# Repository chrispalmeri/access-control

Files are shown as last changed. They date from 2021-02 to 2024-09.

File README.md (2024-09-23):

# doorctl

DIY door access control system with NanoPi

Software part is very much unfinished

<!--

order spare inventory parts

board changes:
  put 12V at the top, move lock?
  you meant to widen lock trace
  you could make the JLCJLC text bigger
  and the github text
  any way to get the resistor designators readable? smaller?
  upsidedown ethernet kinda bugs me

python
  update docs
  totp

-->

# Hardware

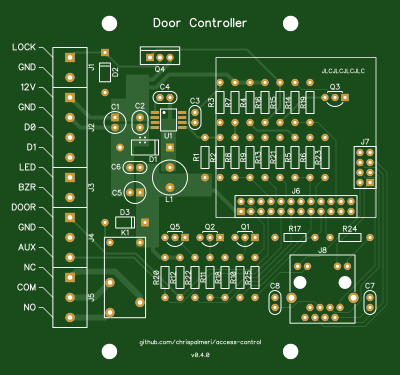
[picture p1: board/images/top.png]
Board picture


[DipTrace][1] files, `gerber.zip` works with [JLCPCB][2]

Removed SVG's from repo but you can drop `gerber.zip` into [tracespace][3] to generate.

You need to plug a [NanoPi Neo Core][4] on to it

  [1]: https://diptrace.com/
  [2]: https://jlcpcb.com/
  [3]: https://tracespace.io/view/
  [4]: https://www.friendlyelec.com/index.php?route=product/product&path=69&product_id=212

These are the gpio pins that are used:

Name | Physical | libgpiod | Type | Description
---  | ---      | ---      | ---  | ---
PA1  | 22       | 1        | OUT  | lock
PG8  | 16       | 200      | OUT  | relay out
PG9  | 18       | 201      | OUT  | reader led
PA6  | 12       | 6        | OUT  | reader buzzer
PA3  | 15       | 3        | IN   | reader d0
PG11 | 7        | 203      | IN   | reader d1
PG6  | 8        | 198      | IN   | door contact
PG7  | 10       | 199      | IN   | doorbell

# Software

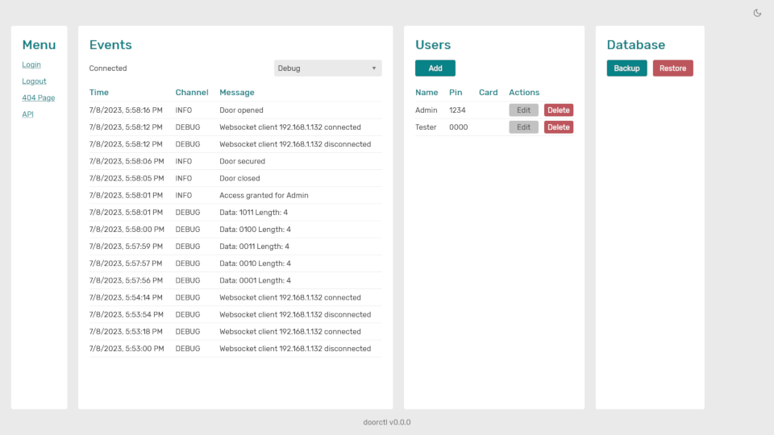
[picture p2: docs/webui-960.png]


## Preparation

Download [Armbian][5] Bullseye CLI image (get the latest archive version),
use [Etcher][6] to flash the image onto your [SD card][7].

Install the SD card and power up the board.

  [5]: https://www.armbian.com/nanopi-neo/
  [6]: https://etcher.balena.io/
  [7]: https://www.westerndigital.com/products/memory-cards/sandisk-ultra-uhs-i-microsd#SDSQUA4-032G-GN6MA

## First boot

Use [Windows Terminal][8] to `ssh root@nanopineo` and login with password `1234`.

* enter new root password twice
* pick `1` for "bash" terminal
* enter new username (e.g. `doorctl`)
* password twice
* display name
* `Enter` to accept language based on detected timezone
* pick `1` for "en_US.UTF-8"
* Run `armbian-config`
    * Personal > Hostname > type a new hostname (e.g. `doorctl-dev`) > Ok > Back
    * System > Install > Install/Update the bootloader on SD/eMMC > Yes
    * System > Install > Boot from eMMC - system on eMMC > Yes > ext4 > Power Off

Unplug power, Remove SD card.

  [8]: https://apps.microsoft.com/store/detail/windows-terminal/9N0DX20HK701

<!--
I think you could then reuse the SD card on additional boards
and only need to do the hostname, bootloader, eMMC steps
-->

## Installation

Connect all your door hardware, reconnect power.

Reconnect over SSH using new username and new hostname.

`sudo apt update`

`sudo apt upgrade`

### Option 1: On device

Over SSH connection:

`git clone https://github.com/chrispalmeri/access-control.git`

`cd access-control`

`sudo ./install.sh`

`sudo shutdown -r now` to reboot

> I'll have to build releases on GitHub or something if using Svelte.
> Otherwise you'll have to `npm install` and `npm build` on device.

### Option 2: Remote development

On Windows host:

`git clone git@github.com:chrispalmeri/access-control.git`

Setup [VS Code][9] and open folder. Enable SFTP extension.

Ctrl-Shift-P > SFTP: Upload Project

Click SFTP icon in sidebar, then click icon on connection to open terminal

`curl -s https://raw.githubusercontent.com/chrispalmeri/access-control/master/install.sh | sudo bash`

`sudo shutdown -r now` to reboot

<!--
reboot maybe should be part of the script?
printing IP address should also be part of the script
-->

Run `sudo systemctl restart doorctl` over ssh whenever you make backend changes.

Run `npm run build` locally after making frontend changes.

  [9]: https://code.visualstudio.com/download

## Usage

Navigate to IP address in browser.

<!--
If events shows wrong contact status and wiegand readding errors

remote in `nano access-control/backend/config.py`
change pin numbers to correct ones for your board
Ctrl+S, Ctrl+X
`sudo systemctl restart doorctl`

I think it has the 60 sec websocket hang when stopping again
just wait a minute and then it is good
-->

Swipe a card and check the events for the number, then add it to a user.

Should be good to go. Check that the hardware is all working correctly.

## Advanced usage

`1` on keypad before credential to toggle persistent unlocked state.
`2` to trigger aux relay.

## Troubleshooting

Restart process with `sudo systemctl restart doorctl`

Check for errors with `sudo journalctl -u doorctl --since "5 minutes ago"`

You can also stop the service and run it from the command line, to easier see
the output. The app will be on port `8080` though instead of `80`

`sudo systemctl stop doorctl`

`sudo systemctl stop doorctl.socket`

`cd ~/access-control/backend/`

`python3 serve.py`

## Update

<!-- assuming on device, otherwise you can just SFTP: Upload Project again -->

`cd access-control`, `git fetch` then `git status`

If there are updates `git pull`.

Maybe should `sudo ./install.sh` again? Might stop service first, delete database if you want to see that created, ignore reboot message after install.

`sudo systemctl restart doorctl`

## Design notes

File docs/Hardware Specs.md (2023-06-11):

# Specs

## FAQ

Q. Why not a microcontroller? It would make interrupts simpler and lower your power
requirements dramatically. And you don't really need a web server on device.

A. Networking, while possible, is more complicated and has minimal feature set.
TLS is the same story, but even more compromises, and super hard to find good
guides, especially for stuff like MQTT or websockets.

## Pins

Inputs are normally high, outputs are normally low.

Name  | Type | Phys | Nano | #     | Orange | #
---   | ---  | ---  | ---  | ---   | ---    | ---
LOCK  | OUT  | 22   | PA1  | 1     | PA2    | 2
RELAY | OUT  | 16   | PG8  | 200   | PC4    | 68
LED   | OUT  | 18   | PG9  | 201   | PC7    | 71
BZR   | OUT  | 12   | PA6  | 6     | PD14   | 110
D0    | IN   | 15   | PA3  | 3     | PA3    | 3
D1    | IN   | 7    | PG11 | 203   | PA6    | 6
DOOR  | IN   | 8    | PG6  | 198   | PA13   | 13
AUX   | IN   | 10   | PG7  | 199   | PA14   | 14

For the pin designators like `PG7` the `P` just means "pin", then each following
letter represents a group of 32 pins. So multiply the zero-indexed letter of the
alphabet position by 32 and add the number to get the final number. And they
were all on `gpiochip0` in my limited experience. For example:

`PA3` would be `0 * 32 + 3` so `gpiochip0 3`

`PG7` would be `6 * 32 + 7` so `gpiochip0 199` 

## Nano Pi

  * Power in is 5V 2A (4.7V-5.6V)
  * All 5V pins are connected
  * pins are 3.3V, output current is 5mA - this is just for calculating NPN/mosfet saturation
    although I think you applied it to input current also

## Reader

  * Power is 12V 80mA
  * Data pins are 5V normally high
  * BZR needs to sink ~ 4.8V 3.6mA
  * LED needs to sink ~ 3.5V 0.4mA
  * Three data resistors achieve pullup plus voltage divide (and current limiting?)
  * I think you have one reader that is 26 bit and the other is 34 bit

## Lock

  * Power is 12V 240mA
  * what is the mosfet saturation?

## Relay

  * Power is 5V 80mA
  * coil has no polarity
  * Can switch at least 3A at 250VAC or 30VDC
    (otherwise check sheet, can do more on NO, especially with AC)

## Contacts

  * Board is not powering, resistor divider is,
    and contact closure just sinks to ground
  * Normal alarm contacts are electrically NO, plus magnet, for a NC alarm loop

## Power

Wired, with battery backup:

  * Mean Well GST25A12-P1J - 12V 25W GST Series Desktop Adaptor Power Supply
  * https://www.aliexpress.us item "12V2A 22.2W UPS Uninterrupted Backup Power Supply Mini Battery For Camera Router"

POE:

  * https://www.amazon.com/dp/B08HS4NT13 Gigabit PoE Splitter 12V 2A Output 802.3af/at 5.5x2.1mm DC Plug PS5712TG

## Misc

  * 22 guage wire https://4rcustomswire.com/products/22-gauge-txl-wire-6-solid-colors-each-10-foot
  * HES 5000 LBM https://www.bsasi.com/hes-5000-lbm

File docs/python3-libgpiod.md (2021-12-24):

https://git.kernel.org/pub/scm/libs/libgpiod/libgpiod.git/

`sudo apt install python3-libgpiod`

Usage `sudo python3 test.py`

`python3 -c 'import gpiod; help(gpiod)' >> help.txt`

---

```
inputs = chip.get_lines([d0, d1, door, aux])

print('offset: {} timestamp: [{}.{}]'.format(
    event.source.offset(),
    event.sec, event.nsec
), end='')

def print_values(lines):
    vals = lines.get_values()

    for val in vals:
        print(val, end=' ')
    print()
```

LineBulk was messing up get/set value and directed everything to the first line so removed
although get_values all together seemed fine
but possibly that relates to the way you could not read interrupt pins values?

---

check if a module exists from command line

`python3 -c 'import state'`

---

can do *args but that's a tuple
**kwargs means the args should be like key=val
the actual names don't matter

---

# does this take care of Ctrl+Z?
# i would rather manually kill the pid
import signal
import os

def handler(signum, frame):
    print('Ctrl+Z pressed, but ignored')
    os.system(f'kill -STOP {os.getpid()}')

signal.signal(signal.SIGTSTP, handler)

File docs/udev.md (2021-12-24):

`man udev`
`man udevadm`

get device info for making rules

`udevadm info -a /dev/gpiochip0`

"looking at device" will have the path
which you can use with `udevadmin test xxxx`
although this is not super useful

```
# /etc/udev/rules.d/99-custom.rules

SUBSYSTEM=="gpio", GROUP="gpio", MODE="0660"

```

`udevadm control --reload` won't change existing devices,
you have to reboot

check permissions

`ls -al /dev/gpiochip*`

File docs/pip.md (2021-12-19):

# pip

Package "python3-aiohttp" has old bug where background tasks are cancelled
before `app.on_shutdown` and `app.on_cleanup` run so they have no effect.

`sudo apt-get install -y python3-pip python3-dev`

`sudo pip3 install --system setuptools wheel aiohttp`

Not using pip "gpiod" because it is not the same as package "python3-libgpiod",
it does not have the same methods.

## Example

```
while keepon:
    await read(app)
```

```
async def shutdown(app):
    global keepon
    keepon = False
    await app['my_task']
```

```
app.on_shutdown.append(reader.shutdown)
```

However, `lines.event_wait()` can still raise "InterruptedError" no matter
how cleanly you do everything else, so I kinda don't care.

Using the packages and catching any errors is simpler, since the gpio interrupts
will get force stopped anyway.

## Future

The latest version (pip) of aiohttp takes 60 seconds to stop because it is
waiting for you to close websockets before it forces it. The package version bug
handily kills everything right away.

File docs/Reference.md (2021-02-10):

# Reference

## Dimensions

caps - 5mm dia 2mm leads

diode - DO-15 

----------

you are using a 10 mil grid

.004 - .008 inch larger than the actual dimensions (same for holes)

> you were doing 0.01 each side

----------

* min trace 3.5mil
* clearance 3.5mil

* min via 8mil inner 18mil outer
* clearance 5mil

* drill hole 8mil to 0.248
* Tolerance ± 3mil
* ring thickness > 3mil

> you are  gonna add 8mil then round to drill size

.08 pads seem good

trace to outline 8mil

--------------

.0465 - mosfet and connectors

.028 - everything else

--------------

https://www.pcbwizards.com/Drillchart.htm

https://www.4pcb.com/trace-width-calculator.html

## Classes

net classes have more info in PCB. Can back annotate schematic, change,
then update from related scematic in pcb

## Moving markings

select "View \ Component Markings \ Move Tool"

## Exporting

### BOM

In Schematic go to Objects > Bill Of material > Export to file (group by name/value)

### Gerber

Just click Export > Gerber and hit the "Export All" button

Select "Zip Archive: Gerber + NC Drill"

### PDF

temporarily set all Trace Color > By Layers when printing to pdf

### SVG

left out Top Paste when dropping into tracespace.io for svg's
(should prob remove paste from the power IC footprint)

> removed two transforms in bottom.svg to get it right side up

drag the svg's into GIMP and set at 100 pixels per inch

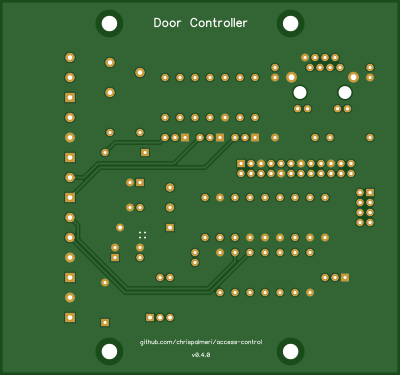
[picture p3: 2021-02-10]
board/images/bottom.png

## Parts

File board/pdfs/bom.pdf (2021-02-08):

Name | Value | Quantity | RefDes | Manufacturer | Part Number
CAP_E | 47uF | 1 | C1 | Nichicon | UVR1V470MDD1TD
CAP_C2 | 10uF | 1 | C2 | TDK | FG11X7R1H106KRT06
CAP_C1 | 2.2nF | 1 | C3 | TDK | FG18X7R1H222KNT00
CAP_C1 | 10nF | 1 | C4 | TDK | FA18X7R1H103KNU00
CAP_E | 100uF | 1 | C5 | Nichicon | UVR1A101MDD1TD
CAP_C1 | 1uF | 1 | C6 | TDK | FG18X7R1E105KRT00
CAP_C1 | 100nF | 2 | C7, C8 | TDK | FG14X7R2A104KNT06
DIODE_S | SB240 | 1 | D1 | Vishay | SB240-E3/54
DIODE | 1N4007 | 2 | D2, D3 | Vishay | 1N4007-E3/54
CON_2P | 2 Screw | 2 | J1, J3 | Phoenix Contact | 1729128
CON_4P | 4 Screw | 1 | J2 | Phoenix Contact | 1729144
CON_3P | 3 Screw | 2 | J4, J5 | Phoenix Contact | 1729131
HDR_2x12 | 2x12 Female | 1 | J6 | 3M | 929975-01-12-RK
HDR_2x4 | 2x4 Female | 1 | J7 | 3M | 929975-01-04-RK
ETH_MAG | Ethernet Mag | 1 | J8 | Pulse | JD2-0010NL
RELAY | 5V SPDT | 1 | K1 | Omron | G5Q-14-DC5
INDUCTOR | 33uH | 1 | L1 | Coilcraft | RFC0810B-333KE
NPN | 2N2222A | 4 | Q1, Q2, Q3, Q5 | ON Semiconductor | PN2222ATA
MOSFET_P | NDP6020P | 1 | Q4 | ON Semiconductor | NDP6020P
RES | 52k3 | 1 | R1 | Yageo | MFR-25FBF52-52K3
RES | 10k | 6 | R2, R4, R7, R10, R11, R14 | Yageo | MFR-25FBF52-10K
RES | 8.2k | 1 | R3 | Yageo | MFR-25FBF52-8K2
RES | 2.2k | 3 | R5, R8, R16 | Yageo | MFR-25FBF52-2K2
RES | 4.3k | 9 | R6, R9, R13, R15, R17, R18, R19, R21, R23 | Yageo | MFR-25FBF52-4K3
RES | 2.4k | 3 | R12, R20, R22 | Yageo | MFR-25FBF52-2K4
RES | 56R | 2 | R24, R25 | Yageo | MFR-25FTE52-56R
POWER_IC | ACT4065ASH-T | 1 | U1 | Qorvo | ACT4065ASH-T

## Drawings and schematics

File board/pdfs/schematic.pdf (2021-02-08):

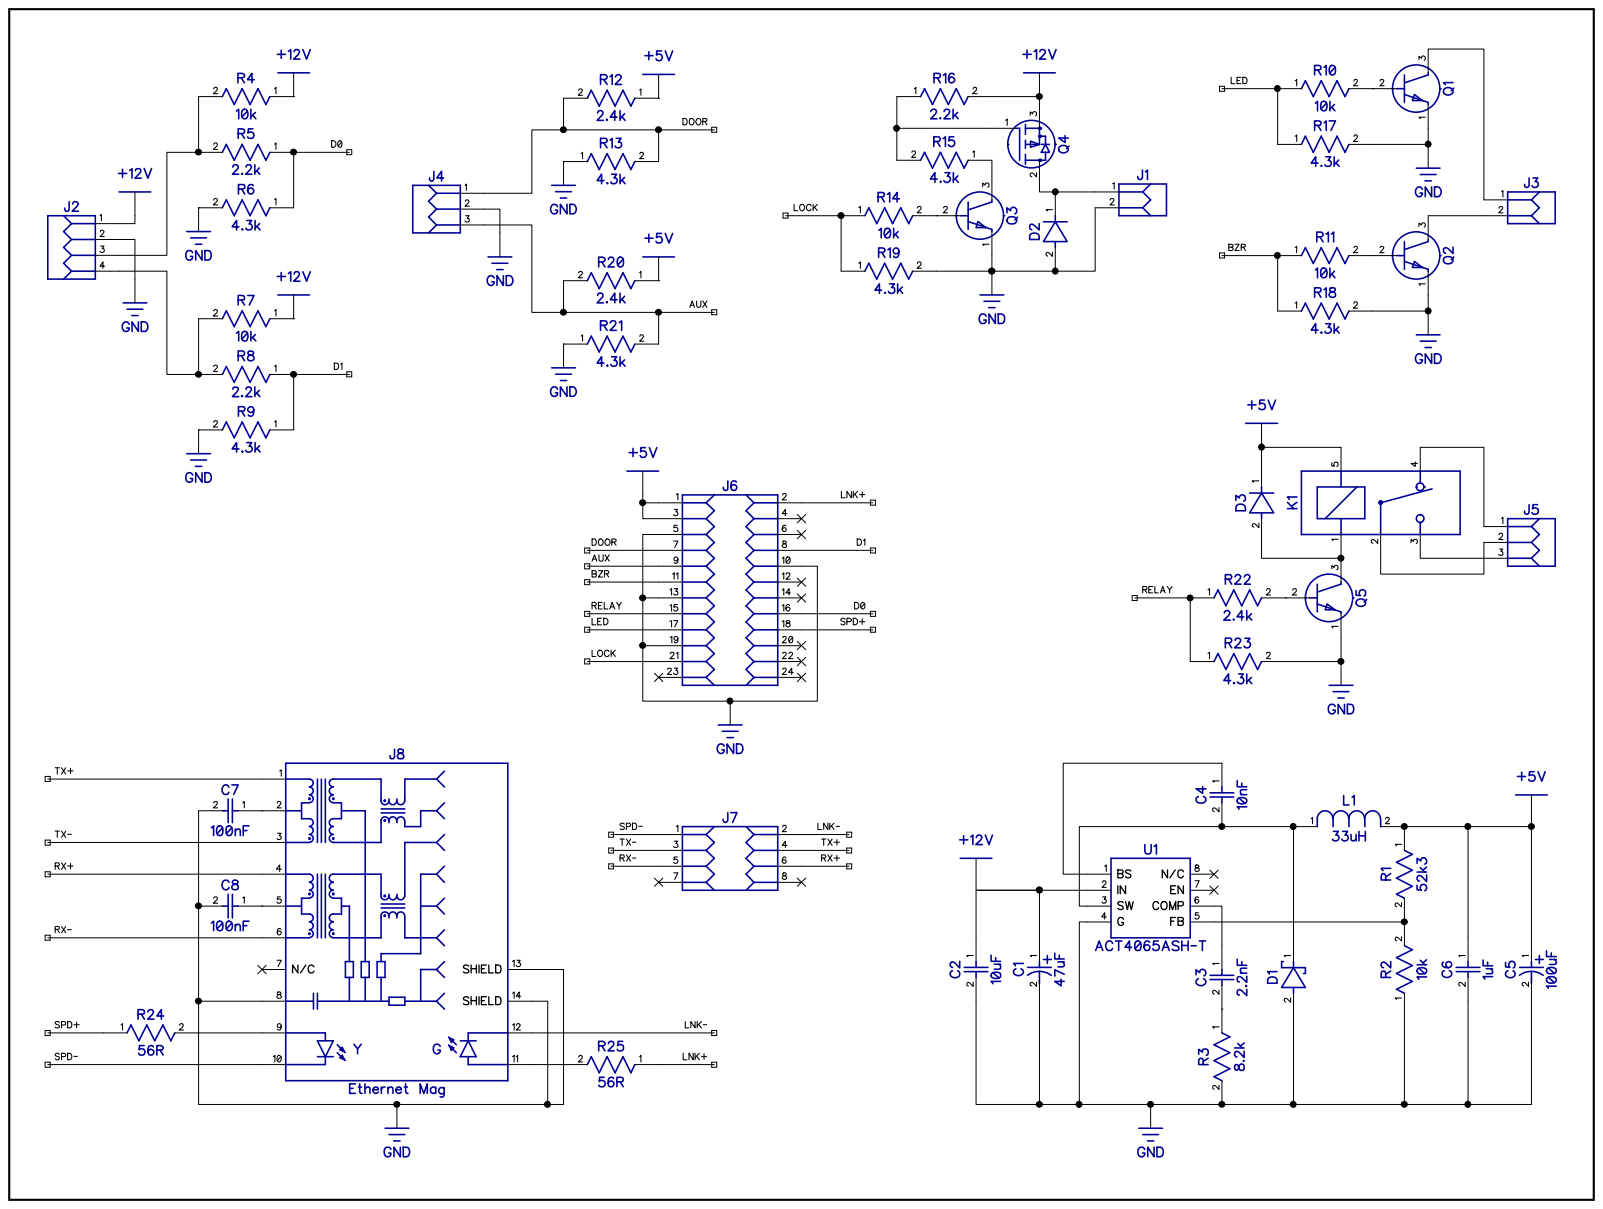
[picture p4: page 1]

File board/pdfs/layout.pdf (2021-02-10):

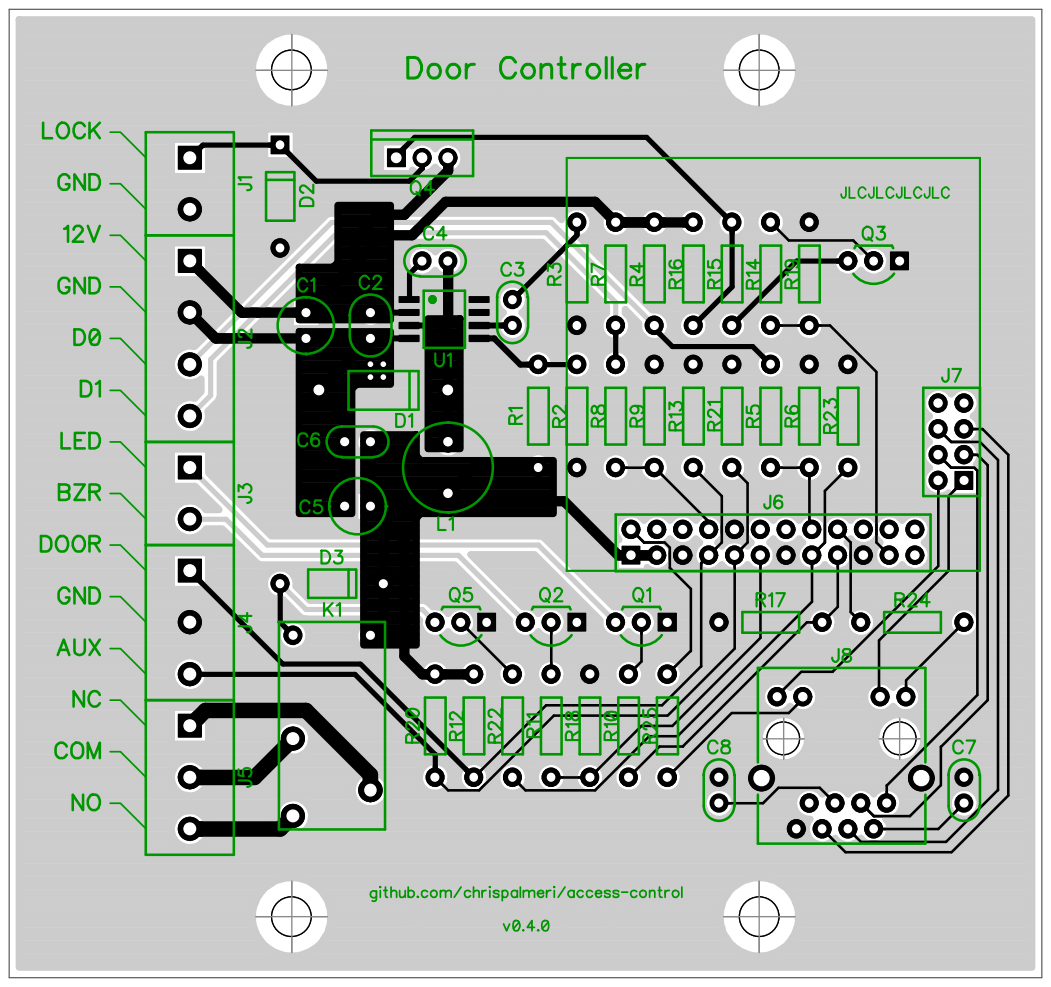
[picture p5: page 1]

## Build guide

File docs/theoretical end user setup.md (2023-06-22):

# theoretical end user setup

plug it in

go to some url which will auto discover it, and save ip

setup login creds (or sync to controller)

enter a friendly name, which autogenerates hostname

save, which shows timer and reboots, and redir to ip

firmware update available - apply

swipe unregistered card

go to add user, pick use last card

# settings

sync with controller, enter ip
use static ip

NO/NC for door
NO/NC for aux
fail safe/secure for lock
use relay as lock/aux
NO/NC relay
use buzzer

lock timeout
use door forced
door left open time

mqtt server address
email notifications
ssl cert

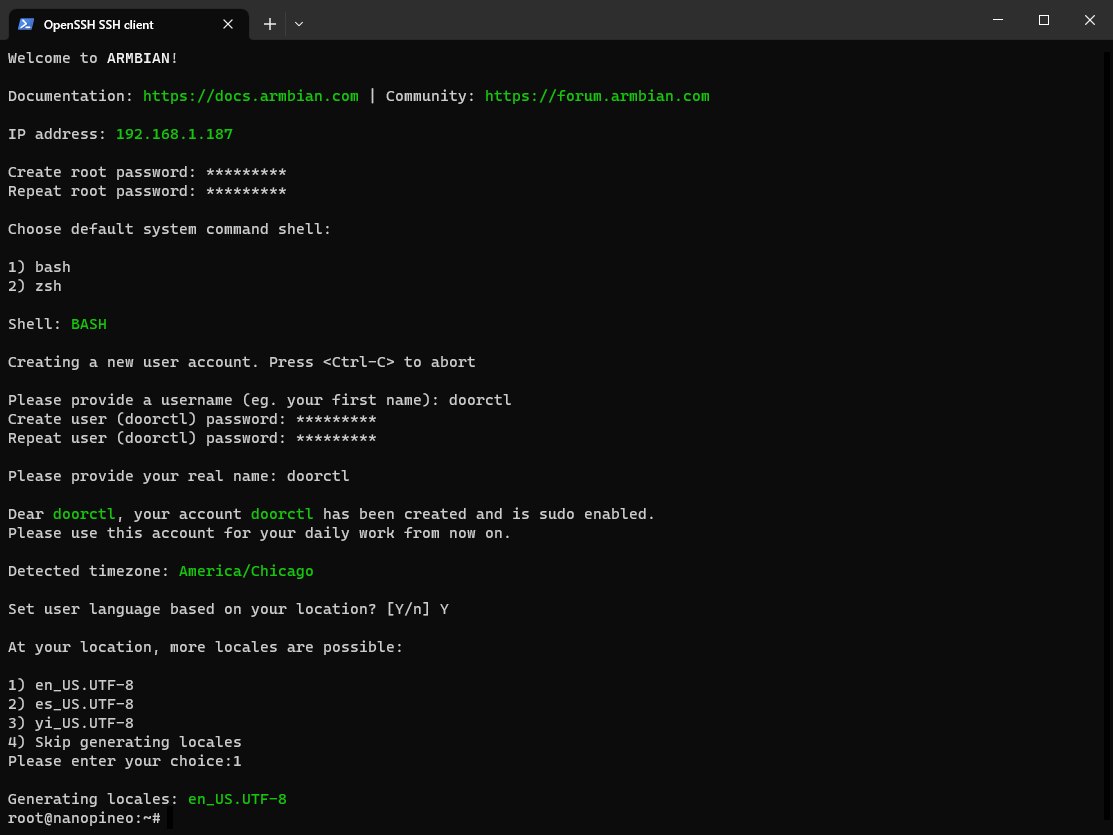
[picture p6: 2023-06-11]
docs/setup.png

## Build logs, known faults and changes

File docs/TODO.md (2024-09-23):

# To do

https://pages.nist.gov/800-63-3/sp800-63b.html#reqauthtype

revealable password field

per user salt
10,000 rounds pbk

+1 round using server secret salt, not stored in db

https://docs.python.org/3/library/hashlib.html#key-derivation

https://www.slingacademy.com/article/python-ways-to-hash-a-password/#Three_Ways_to_Hash_a_Password

https://github.com/OWASP/CheatSheetSeries/blob/master/cheatsheets/Authentication_Cheat_Sheet.md

https://scotthelme.co.uk/boosting-account-security-pwned-passwords-and-zxcvbn/

---

`apt get install python3-pyotp` https://github.com/pyauth/pyotp

need to store random_base32 in db

store last timestamp and code (or hash of code) to deny using the same one again

## Layout Changes

  * add connection diagram or image
  * check that diptrace setup is repeatable
  * brief directions, plus link to Mouser project

## Code changes

endpoints to loose and secure
you could add "Last Denied Pin" button to users dialog now if you wanted

show database size - also is there a memory limit or anything?

  * DEBUG messages for user edited, user deleted
  * "Connected" styling
  * add database restored event log - at least show if restore completed, currently no feedback
    * obviously refresh events afterward
  * refactor events (differentiate specific status from operational event)
    * entry made, door propped, door forced - independent of door open/close
    * lock unlocked/locked - independent of user validated
    * led on, led off
    * buzzer
    * login/logout
    * http?
  * if it gets laggy then edit webhook to send event - so web does not need to hit api every time
    * pretty sure that won't happen and the complexity to keep the ui accurate won't be worth it
  * rename event channels like physicalAccess,remoteAccess,serverStatus,hardwareStatus,humanResources,codeDebug
  * user export/import csv
    * so, basically just break db backup/restore into two - users, and events - that's all that is is the db anyway
  * include state in websocket data instead of generic notification
  * 'gpio' package, change 'entry' to 'output'
  * increasing timeout for bad pin or card attempts
  * reboot command
  * upgrade command
  * beep or something on startup, so you know when it is ready after a power cycle
  * add control buttons on homepage, would need api first
  * way to delete events
  * websocket connects/disconnects when firefox scrapes a page preview - auth would stop that

## Dev setup

  * move `install.sh` into `backend/` ?
  * log ip address
  * smarter install/update script depending on what changed
  * split docs/make consistent for each windows dev, orange pi stage, nano pi prod
  * add git cheatsheet to various-scripts repo

## Ideas

  * make a simple and an advanced version, neo is cheaper than neo core
  * slim project box instead of in-wall
  * use 3.3 from board instead of 5v divider on contacts
  * transistor or resistor arrays

Would it be possible to go to doorctl.com
and have it connect websockets to any devices on local network?
and somehow sign in to all of them
that would be super cool

---

aiohttp want you to do state like this
but your 'device' stuff is pretty separated from 'app'

```py
app['database'] = conn
app['broadcaster'] = broadcast
```
---

dip switch to send 12V to relay?
also, both 12V jack and terminals next to each other
label the switch with "double check your power draw first"

---

here's a werid thing, the socket can still be up, but api down,
cause of name resolution I guess, like network switch is up but router is down

--- 

https://packages.ubuntu.com/search?suite=default&section=all&arch=any&keywords=aiohttp&searchon=names

https://github.com/maximdanilchenko/aiohttp-apispec

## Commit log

2019-09-16 Restructure and add resources
    [BoardOutline.gbr, Bottom.gbr, BottomAssy.gbr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]
2019-09-17 Update directory structure
    [BoardOutline.gbr, Bottom.gbr, BottomAssy.gbr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]
2019-09-18 Relink schematic and layout
2019-09-26 New double gang board layout
    [BoardOutline.gbr, Bottom.gbr, BottomMask.gbr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]
2019-09-26 Move datasheets and add svgs
    [BoardOutline.gbr, Bottom.gbr, BottomAssy.gbr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]
2019-10-05 Update pins to match new board
2021-01-31 Redo circuit layout
    [bom.csv]
2021-01-31 Add back mounting holes
2021-01-31 Update silkscreen
2021-02-01 Tweaks and add pdfs
    [bom.csv]
2021-02-01 Update gerbers
    [Bottom.gbr, BottomMask.gbr, BottomSilk.gbr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]
2021-02-01 Add back ref des markings
    [TopSilk.gbr]
2021-02-02 Make schematic readable
2021-02-02 Reduce amount of tracked files
    [BoardOutline.gbr, Bottom.gbr, BottomAssy.gbr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]
2021-02-03 Add bom pdf and notes
2021-02-08 Update connectors and bom
    [bom.csv]
2021-02-08 Clean up schematic
2021-02-10 Update pin numbers
2021-12-24 A couple more notes
2023-06-11 Auto detect board type
2023-06-24 Button and input styling
2023-06-25 Button styling
2023-06-28 Package device related modules
2023-07-06 Socket session check
